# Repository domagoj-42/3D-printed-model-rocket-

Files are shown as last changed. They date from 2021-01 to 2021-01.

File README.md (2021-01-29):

# 3D-printed-model-rocket-

This repository contains the 3D models, code and schematics for a 3D printed model rocket which has a GY-87 sensor module with an Arduino Pro Mini mounted in the payload compartment. The data is recorded on an Adafruit OpenLog module. Furhermore, it includes a Python data analysis program which converts the data to usable units and plots it. This data comprises of 3-axis accelerometer, gyroscope, magnetometer pressure and temperature data. The Python program includes acceleration matrix rotation using the gyroscope from the sensor's local frame of reference to the global one, as well as calibration value calculation, from which Z-axis gravity offset may be subtracted. Via integration the velocities and distances are derived, and plotted.

Technical information:
- Arduino libraries: i2cDevLib libraries for MPU6050, HMC5883L and BMP085
- Python dependancies: pandas, numpy, scipy and matplotlib
- 3D prining material used: PETG
- The rocket has MASS grams using PETG, which is a high amout of mass for its size, so the delay for deploying the parachute should be small. a B6-2 engine did not deploy the parachute on time, but a C6-3 engine worked fine. 

Rocket Assembly Instructions:
- 3D print all parts (you may wish to use translucent material for the payload compartment to see the indicator loghts)
- the fueselage is glued to the engine assmebly
- the parachute dimensions used for 143 grams: The radius of the vent hole is 4 cm, the length of the canopy is 19cm, and the length of the attachment section is 1cm. In total, the tarp has a 24cm radius, that is, a diameter of 48cm.
- internally, a rope is used to connect the bottom of the payload compartment to the fuesalage, which connects to the parachute
- you may wish to add insulation tape to the fuselage - payload compartment connection to increase friction
- payload and engine mounted, nose cone and engine cap screwed in
- hot glue shout be applied to where the rope comes through the payload compartment to prevent the gasses venting through the holes.

Issues with current design:
- insufficient ventilation in payload compartment for consistent temperature measurements
- very high drift after integration

Electronic payload information
- GY-87
- Arduino Pro Mini from SparkFun
- OpenLog from SparkFun
- dd05cvsa_05 charge controller
- generic 90 mAh LiPo battery
- electronics are seperated into 3 circular PCBs - the top one contains the OpenLog and serial wire breakouts that connect to the serial line. A 4-switch dip switch is present, 2 switches intersecting the serial line's connection to the OpenLog (you cannot upload via serial flasher and have OpenLog connected to the serial line, so this switch is used), and one switch connected to one of the battery's terminals. On the central board is the GY-87 module. On the bottom board is the Arduino Pro Mini and charge controler.
- shematic.png contains the wiring diagram
- in the existing design, a nylon standoff was added to prevent the SD card from getting bumped out (see shematic for details)

Things to note:
- config.txt is the config file for the OpenLog module, copy it to the SD card or change the baud rte on your config file to the appropriate one from the Arduino program

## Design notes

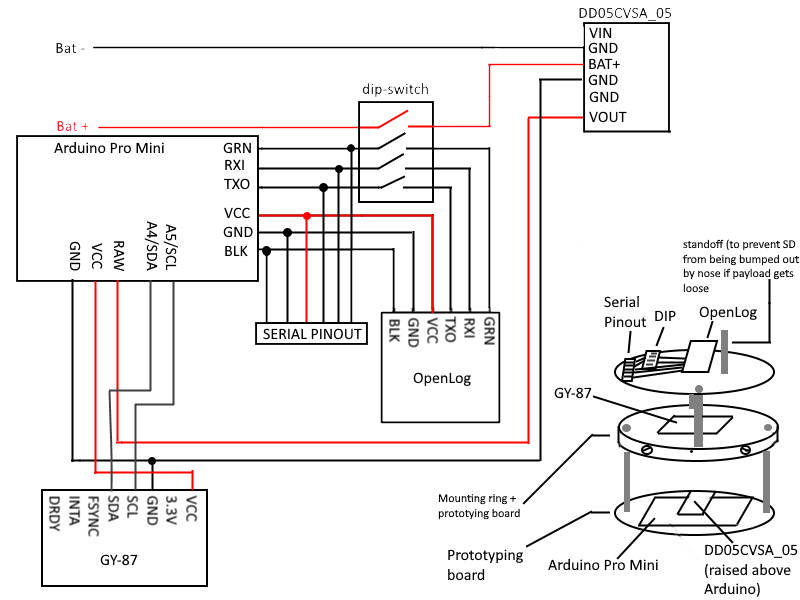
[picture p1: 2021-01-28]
schematic.png

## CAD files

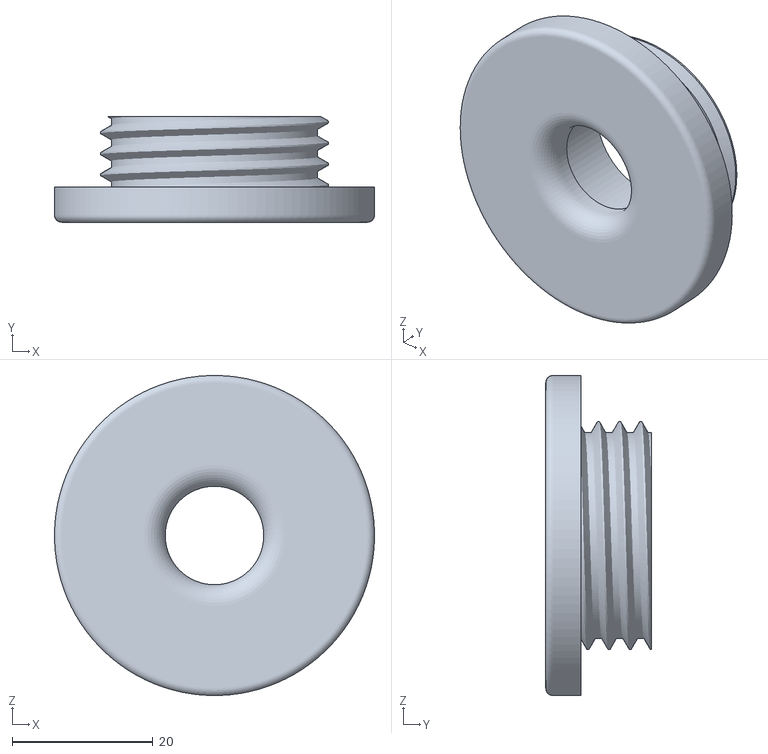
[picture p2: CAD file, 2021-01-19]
engine cap.stl
45.5 x 15.0 x 45.5

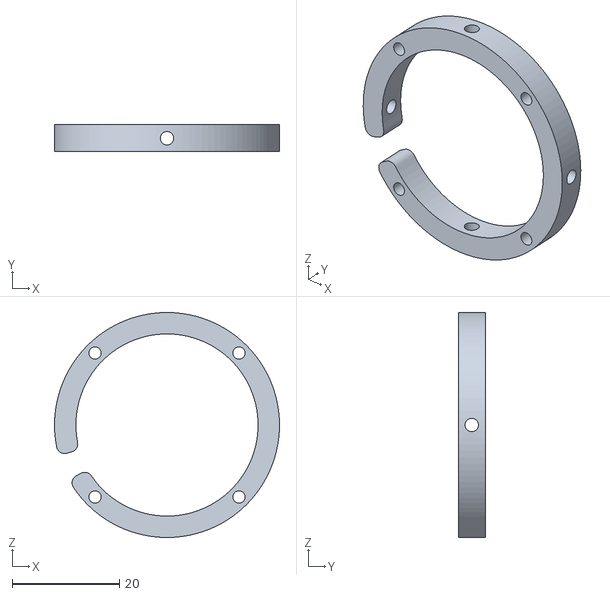
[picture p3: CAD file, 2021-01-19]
component mount.stl
42.0 x 5.00 x 42.0

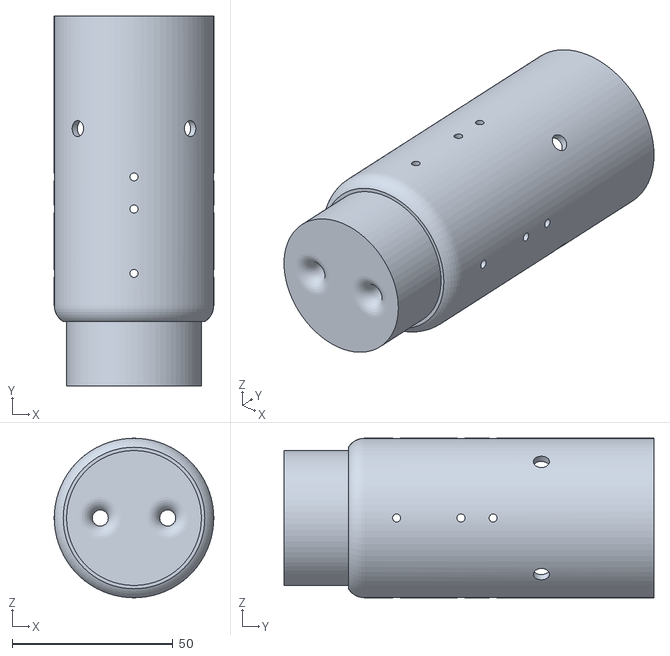
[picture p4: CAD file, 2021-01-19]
payload compartment.stl
49.6 x 115.0 x 49.6

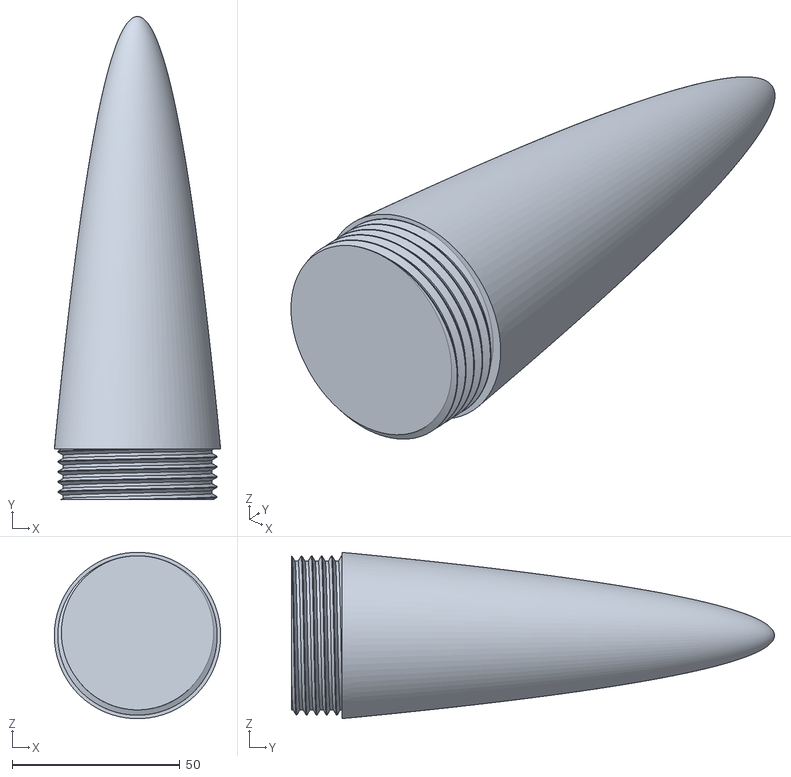
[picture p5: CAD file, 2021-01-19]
nose.stl
49.6 x 143.9 x 49.5

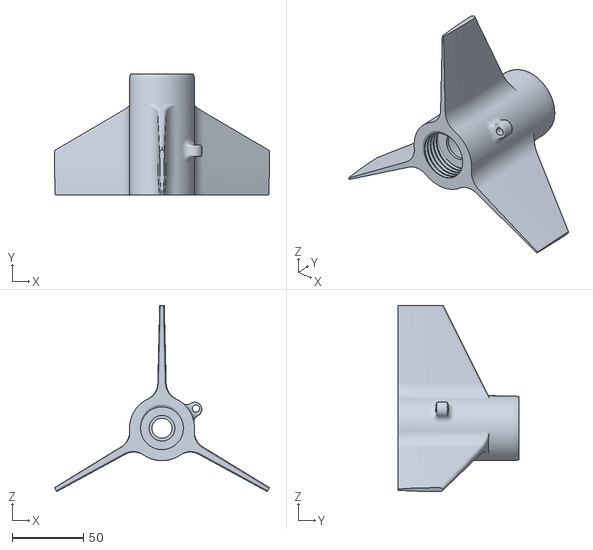
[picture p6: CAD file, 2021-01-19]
engine assebly.stl
150.6 x 85.0 x 130.4

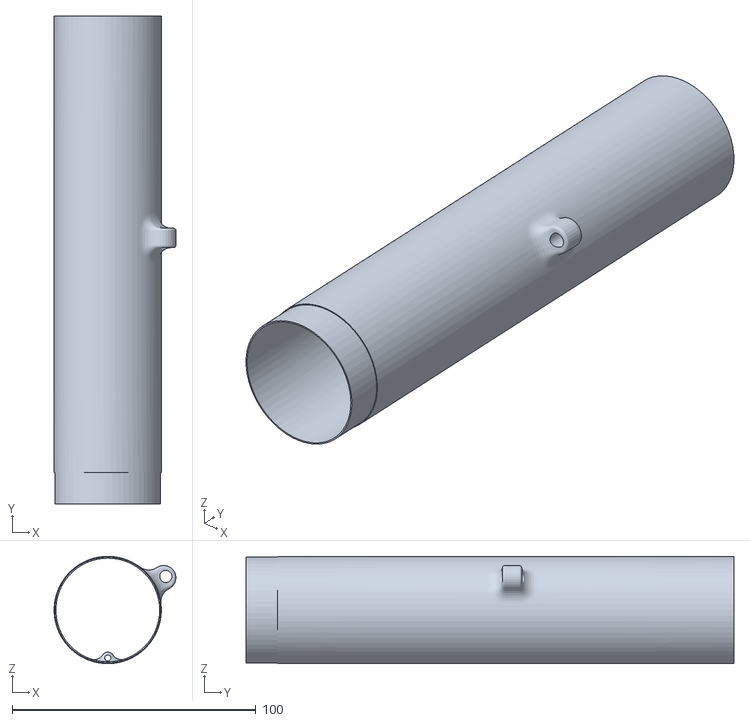
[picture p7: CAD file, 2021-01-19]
fuselage.stl
49.9 x 200.0 x 44.0

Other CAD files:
Model Rocket Version 3 v16.f3d

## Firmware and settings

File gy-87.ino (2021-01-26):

#include "Wire.h"
#include "I2Cdev.h"
#include "MPU6050.h"
#include "HMC5883L.h"
#include "BMP085.h"

MPU6050 accelgyro;
HMC5883L mag;
BMP085 presstemp;

//accelerometer
int16_t ax;
int16_t ay;
int16_t az;
//gyroscope
int16_t gx;
int16_t gy;
int16_t gz;
//magnetometer
int16_t mx;
int16_t my;
int16_t mz;
//barometer/thermometer
float temperature;
float pressure;
float altitude;
//time
unsigned long t; //measurement time
unsigned long reference_time; 

void setup() {
   Serial.begin(57600);   //intitialize serial communication
   Wire.begin();    //initialize i2c communication
   accelgyro.setI2CMasterModeEnabled(false);
   accelgyro.setI2CBypassEnabled(true) ;
   accelgyro.setSleepEnabled(false);

   //initialize sensors
   accelgyro.initialize();
   mag.initialize();
   presstemp.initialize();

   accelgyro.setFullScaleAccelRange(MPU6050_ACCEL_FS_16);
   accelgyro.setFullScaleGyroRange(MPU6050_GYRO_FS_2000);
   mag.setMode(HMC5883L_MODE_CONTINUOUS);

   //test connections
   Serial.println(mag.testConnection() ? "HMC5883L connection successful" : "HMC5883L connection failed");
   Serial.println(accelgyro.testConnection() ? "MPU6050 connection successful" : "MPU6050 connection failed");
   Serial.println(presstemp.testConnection() ? "BMP085 connection successful" : "BMP085 connection failed");
   Serial.println("t\tax\tay\taz\tgx\tgy\tgz\tmx\tmy\tmz\ttemp\tpress\talt");

}

void loop() {
   reference_time = millis();
   if (reference_time - t >= 14){
     //read time
     t = millis();
     
     //read accelrometer and gyroscope
     accelgyro.getMotion6(&ax, &ay, &az, &gx, &gy, &gz);
     
     //read magentometer
     mag.getHeading(&mx, &my, &mz);
     
     //set BMP180 to temperature mode and read temperature
     presstemp.setControl(BMP085_MODE_TEMPERATURE);
     temperature = presstemp.getTemperatureC();
  
     //set BMP180 to pressure mode, read pressure and calculate altitude
     presstemp.setControl(BMP085_MODE_PRESSURE_2);
     pressure = presstemp.getPressure();
     altitude = presstemp.getAltitude(pressure);
  
     //get time just before it is outputted, marks begging of outputting data
     Serial.print(t);
     Serial.print("\t");
  
     // output accelerometer
     Serial.print(ax);
     Serial.print("\t");
     Serial.print(ay);
     Serial.print("\t");
     Serial.print(az);
     Serial.print("\t");
  
     //output gyroscope
     Serial.print(gx);
     Serial.print("\t");
     Serial.print(gy);
     Serial.print("\t");
     Serial.print(gz);
     Serial.print("\t");
  
     //output magentometer
     Serial.print(mx);
     Serial.print("\t");
     Serial.print(my);
     Serial.print("\t");
     Serial.print(mz);
     Serial.print("\t");
  
     //output pressure/temperature
     Serial.print(temperature);
     Serial.print("\t");
     Serial.print(pressure);
     Serial.print("\t");
     Serial.print(altitude);
     Serial.print("\n\r");
   }
}
